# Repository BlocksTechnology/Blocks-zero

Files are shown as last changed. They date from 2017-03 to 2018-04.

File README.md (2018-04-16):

# Blocks zero
In this repository you will find the firmware source code, BOM, STLs of the printed parts and frames for the [Blocks zero 3D printer](http://blockstec.com/zero.html)

# Updating the firmware:
 - Download and install Cura 15.02.1: [Win](http://software.ultimaker.com/old/Cura_15.02.1.exe) / [Mac](http://software.ultimaker.com/old/Cura-15.02.1-MacOS.dmg)
 - Download the [HEX file](http://blockstec.com/downloads/Blocks_zero_1.2.1.hex)
 - Connect your USB printer cable
 - Open Cura and select menu "Machine" -> "Install custom firmware"
 - Select the downloaded HEX file.
 - Wait for the upload to finish and press "OK"

In case the update does not start, please verify the "Serial port" and "Baudrate" (250000) settings in the menu "Machine" -> "Machine settings".

# Changelog:
V1.2.1:
 - Homing after print bug solved

V1.2:
 - USB communication bug solved
 - Baudrate changed to 250000

V1.1:
 - New load/unload filament routine
 - Option to clean the nozzle before bed level
 - Thermal runaway safety feature
 - Filament runout (needs printing new extruder and adding a microswitch to work)
 - Reversed direction of the LCD knob

# License
Blocks one is licensed under a [Creative Commons Attribution-ShareAlike 4.0 International License](http://creativecommons.org/licenses/by-sa/4.0/)

# Firmware
The firmware was based on [Marlin](https://github.com/MarlinFirmware/Marlin) and https://github.com/bq/Marlin

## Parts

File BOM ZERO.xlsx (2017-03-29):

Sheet: BOM zero
 | Bom Blocks Zero
 | ITEM LIST | DESCRIPTION | NOTAS | DATASHEET | LINKS
1 | MEGA 2560 R3 | Arduino
1 | RAMPS 1.4 Board Red For Mega 2560 R3
1 | RepRapDiscount Smart Controller 2004LCD Blue Light
4 | Green A4988 Stepper Motor Driver (+Heatsink,1.5A) | Drivers
3 | NEMA17 Stepper Motor 34mm Long, 1.5A | Motors X,Y,Z
1 | NEMA17 Stepper Motor 40mm Long, 1.2A | Motor Extruder
3 | Bed Spring | Springs for bed
1 | 12V 3010 Cooling Fan | Hotend cooler fan
2 | 12V 5015 Blow Fan | Nozzle/Electronics fan
2 | Bowden Fitting | Fittings PTFE
1 | MK7 Stainless Steel Extrusion Gear | Extruder gear
1 | Closed Loop GT2 Belt - 190 teeth / 380mm | Timming belt for X (hotend)
1 | Closed Loop GT2 Belt - 210 teeth / 420 mm | Timming belt for Y (bed)
2 | 20 teeth GT2 Aluminium Timing Pulley 5mm | pulley X & Y
6 | LM6UU Linear Bearing | X & Y
4 | LM8UU Linear Bearing | Z
12 | Timing Belt Idler Pulley F625Z Flanged Ball Bearing | Idlers
1 | 608ZZ Ball Bearing | Extrusor
2 | High Frequency Chrome Plated Smooth Rod 8mm - 235mm | Z
2 | High Frequency Chrome Plated Smooth Rod 6mm - 200mm | Y
2 | High Frequency Chrome Plated Smooth Rod 6mm - 183mm | X
1 | Acrilic frames | 6 frames
9 | Printed parts
1 | Threaded rod M5 200mm | Z
2 | Black cable guides (50 & 30cm) | Cables |  |  | TME (http://www.tme.eu/en/details/cyg-pet-10-bk_box/polyester-conduits/cyg/cyg-pet10-box/)
3 | 30 mm silicone tube | Z /fan spacer
2 | 10 mm silicone tube | LCD spacer
1 | DC power jack | 5,5x2,1mm 12V/6A |  |  | https://mauser.pt/catalog/product_info.php?cPath=1874_640_387_1155&products_id=56723
1 | Power switch | 20mm white |  |  | https://mauser.pt/catalog/product_info.php?cPath=324_1401_1402&products_id=66105
20 | Zip ties | white - 100mm |  |  | TME (http://www.tme.eu/en/details/bmb1025/cable-ties/bm-group/)
2 | Bulldog clips | bed clamps
2 | Extruder springs | Extruder
1 | Caixa de junção | fans/ Power |  |  | TME (http://www.tme.eu/en/details/dg235-5.0-02p/pcb-terminal-blocks/degson-electronics/dg235-50-02p-11-00ah/)
1 | Hot End
1 | Autocolantes Blocks logo | Stickers
21 | Etiquetas | Cable tags
1 | Allen key 1.5mm | Bossard |  |  | TME (http://www.tme.eu/en/details/b1.5_bn1169/hex-and-torx-keys/bossard/1380605/)
1 | Allen key 2 mm | Bossard |  |  | TME (http://www.tme.eu/en/details/b2_bn1169/hex-and-torx-keys/bossard/1380613/)
1 | Allen key 2.5mm | Bossard |  |  | TME (http://www.tme.eu/en/details/b2.5_bn1169/hex-and-torx-keys/bossard/m25bn1169/)
1 | Allen key 3mm | Carl Kammerling |  |  | TME (http://www.tme.eu/en/details/ck-441103/hex-and-torx-keys/carl-kammerling/t4411-03/)
 | Screws Nuts Washers
35 | M3 16 mm | Bossard | BN17 |  | TME (http://www.tme.eu/pt/details/b3x16_bn17/cavilhas/bossard/3646125/)
23 | M3 8 mm | Bossard | BN17 |  | TME (http://www.tme.eu/pt/details/b3x8_bn17/cavilhas/bossard/3186761/)
1 | M3 30 mm | Bossard | BN17 |  | TME (http://www.tme.eu/pt/details/b3x30_bn17/cavilhas/bossard/3646128/)
9 | M3 10 mm | Bossard | BN17 |  | TME (http://www.tme.eu/pt/details/b3x10_bn17/cavilhas/bossard/5503267/)
4 | M3 20 mm | Bossard | BN17 |  | TME (http://www.tme.eu/pt/details/b3x20_bn17/cavilhas/bossard/3646126/)
1 | M3 40 mm | Fabory / Bossard | BN613 | FABORY (https://www.fabory.com/pt/fixacao/produtos-sextavados-interiores/parafuso-cabeca-cilindrica-sextavado-interior-din-912-aco-inoxidavel-a2-min-50-m3x40/p/510500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) | TME (http://www.tme.eu/pt/details/b3x40_bn613/cavilhas/bossard/1406795/)
5 | M3 50 mm | Fabory / Bossard | BN613 | FABORY (https://www.fabory.com/pt/fixacao/produtos-sextavados-interiores/parafuso-cabeca-cilindrica-sextavado-interior-din-912-aco-inoxidavel-a2-70-m3x50/p/51050030050) | TME (http://www.tme.eu/pt/details/b3x50_bn613/cavilhas/bossard/1746189/)
4 | M2 8 mm | Bossard | BN11 |  | TME (http://www.tme.eu/pt/details/b2x8_bn11/cavilhas/bossard/m2x8bn11/)
2 | M2 12 mm | Bossard | BN612 |  | TME (http://www.tme.eu/pt/details/b2x12_bn612/cavilhas/bossard/1233726/)
6 | M5 25 mm | Bossard | BN17 |  | TME (http://www.tme.eu/pt/details/b5x25_bn17/cavilhas/bossard/1019783/)
2 | M4 20mm | Bossard | BN17 |  | TME (http://www.tme.eu/pt/details/b4x20_bn17/cavilhas/bossard/1019708/)
50 | M3 nut | Bossard | BN117 |  | TME (http://www.tme.eu/pt/details/b3_bn117/porcas/bossard/1874659/)
7 | M5 nut | Bossard | BN124 |  | TME (http://www.tme.eu/pt/details/b5_bn124/porcas/bossard/m5bn124/)
2 | M2 nut | Bossard | BN109 |  | TME (http://www.tme.eu/pt/details/b2_bn109/porcas/bossard/m2bn109/)
5 | M5 washer | Bossard | BN670 |  | TME (http://www.tme.eu/pt/details/b5_bn670/arruelas/bossard/1253212/)
1 | M5 spacer | Dremec | 5.3x8mm |  | TME (http://www.tme.eu/pt/details/dr3110_5.3x8/espacadores-metalicos/dremec/311053x08/)
 | Cables | Comprimento (cm) | Terminação
1 | Endstop X | 95 cm | Jst e Fim de Curso | https://www.omron.com/ecb/products/pdf/en-d2f.pdf | http://www.tme.eu/pt/details/d2f-01fl/microcomutadores-de-conexao/omron/
1 | Endstop Y | 15 cm | Jst e Fim de Curso | https://www.omron.com/ecb/products/pdf/en-d2f.pdf | http://www.tme.eu/pt/details/d2f-01fl/microcomutadores-de-conexao/omron/
1 | Endstop Z | 15 cm | Jst e Fim de Curso | https://www.omron.com/ecb/products/pdf/en-d2f.pdf | http://www.tme.eu/pt/details/d2f-01fl/microcomutadores-de-conexao/omron/
1 | Fan 30x30 | 95 cm | Preto/vermelho
1 | Blower 5010 | 20 cm | Preto/vermelho
1 | Blower 5010 | 95 cm | Preto/Branco
1 | Motor X | 40 a 70 cm | Normal
1 | Motor Y | 15 a 30 cm | Normal
1 | Motor Z | 15 a 30 cm | Normal
1 | Motor Ex | 40 a 70 cm | Normal
1 | Heater Hotend | 90 a 100 cm | Normal
1 | Sensor temp hotend | 90 a 100 cm | Jst
 | Etiquetas | Código
 | Endstop X | H.4-X
 | Endstop Y | B.4-Y
 | Endstop Z | P.1-Z
 | Blower Peça | J.1
 | Fan hotend | J.2
 | Blower Electrónica | P.7
 | Hotend heater
 | Termistor

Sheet: WEAS cablagem
 | Pedido de Orçamento para Cablagem da BLOCKS zero
 |  | Comprimento (cm) | Terminações | Datasheet
 | Cables
1 | Endstop X | 95 | Jst e Fim de Curso (Com/NC) | https://www.omron.com/ecb/products/pdf/en-d2f.pdf
1 | Endstop Y | 15 | Jst e Fim de Curso (Com/NC) | https://www.omron.com/ecb/products/pdf/en-d2f.pdf
1 | Endstop Z | 15 | Jst e Fim de Curso (Com/NC) | https://www.omron.com/ecb/products/pdf/en-d2f.pdf
 | Conjunto Power | 2x20 cm + 7 cm | 12V/6A requisitos mínimos
1 | DC power plug | ver fotos abaixo | 2 x Soldar e Manga termoretráctil | http://www.cliffuk.co.uk/products/dcconnectors/FC681492.pdf
1 | Power switch white | ver fotos abaixo | 2 x Soldar e Manga termoretráctil | http://www.bulgin.com/media/bulgin/data/A_Rocker%20Switch.pdf
1 | Caixa de junção | ver fotos abaixo | 4 x Soldar e Manga termoretráctil | http://www.degson.com/20081120/epdf/1175.pdf
1 | Ficha verde Ramps | ver fotos abaixo | 2 x Esmagar com parafuso | fornecida com o Ramps

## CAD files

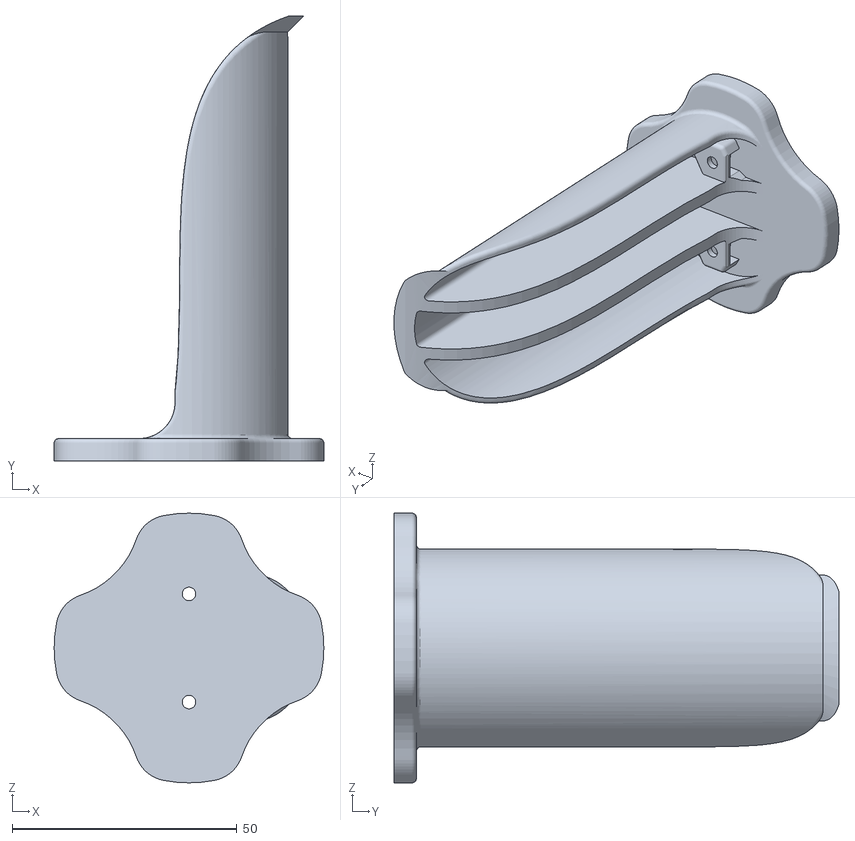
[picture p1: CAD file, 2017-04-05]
STL_Files/Spool V2.stl
60.0 x 99.0 x 60.0

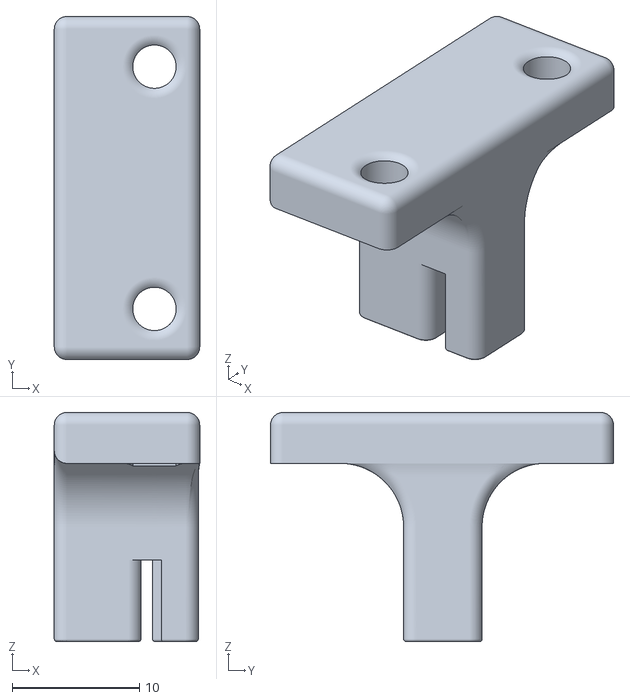
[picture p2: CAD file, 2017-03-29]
STL_Files/belgt fixer Y.stl
11.4 x 26.9 x 18.0

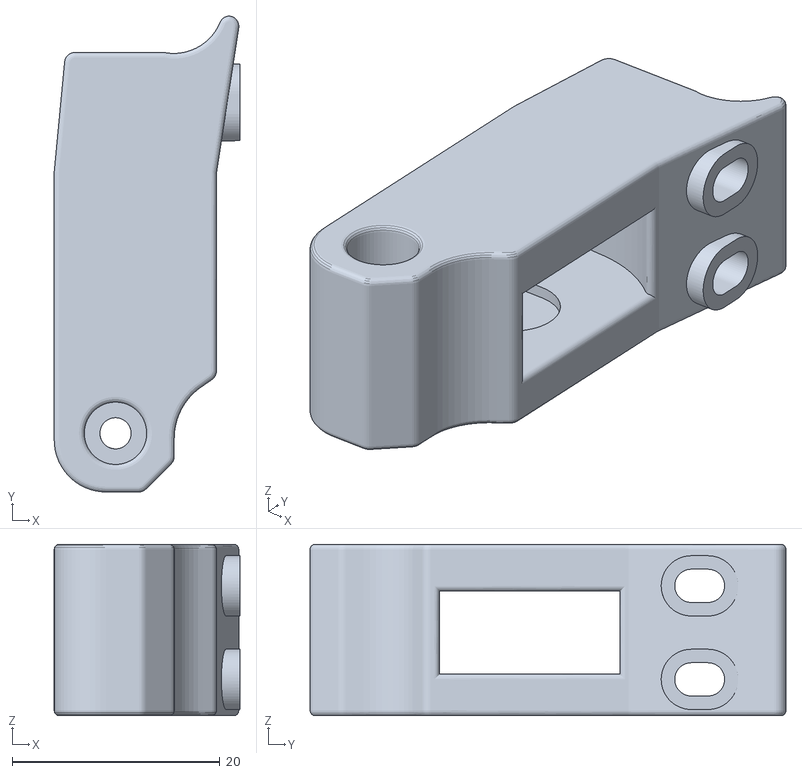
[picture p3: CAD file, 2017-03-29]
STL_Files/Extrusor Idler.stl
17.9 x 45.8 x 16.5

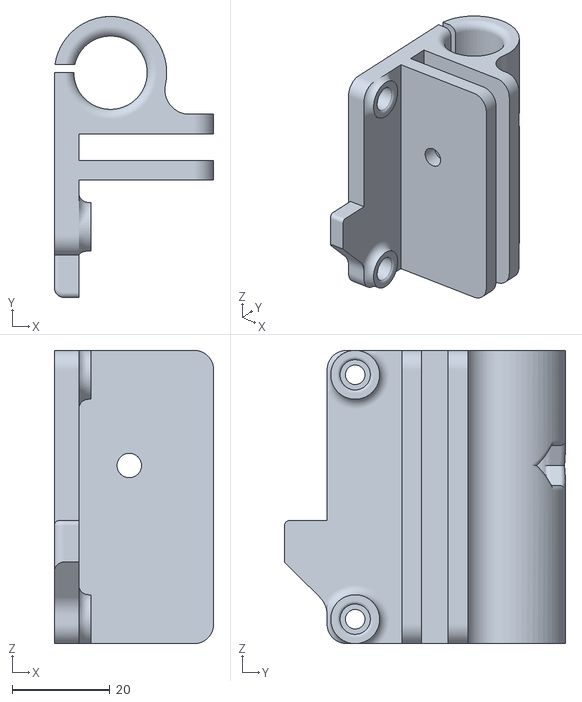
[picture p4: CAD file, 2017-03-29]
STL_Files/XZ left.stl
32.6 x 57.5 x 60.0

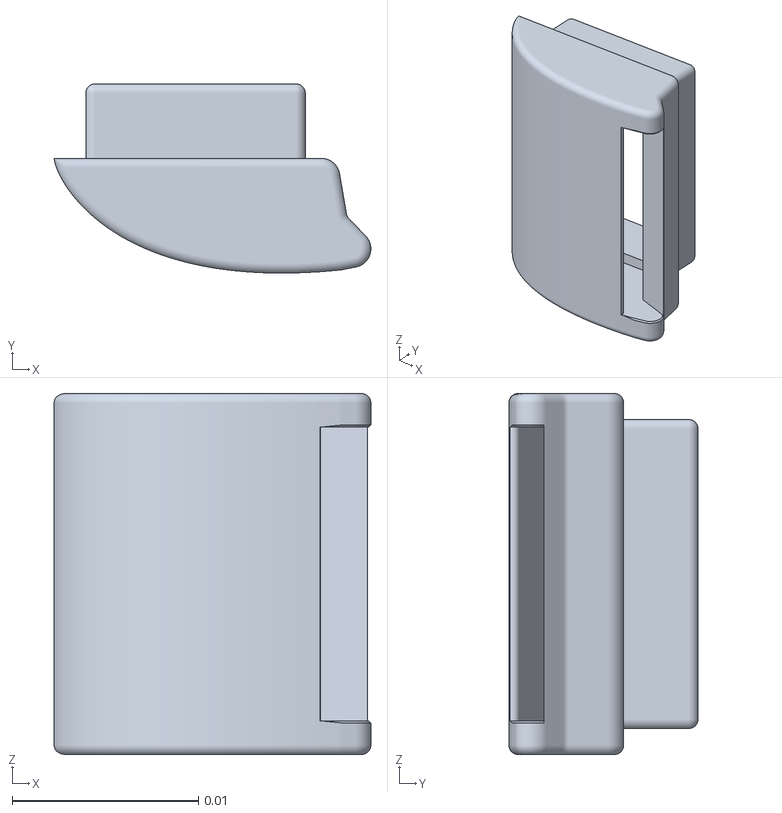
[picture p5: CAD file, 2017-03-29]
STL_Files/Fan Duct.stl
0.017 x 0.0102 x 0.0194

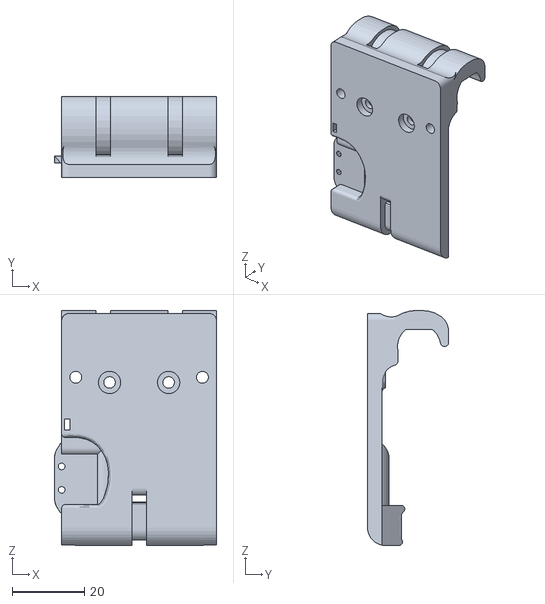
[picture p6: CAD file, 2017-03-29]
STL_Files/X carriage.stl
45.0 x 22.5 x 65.2

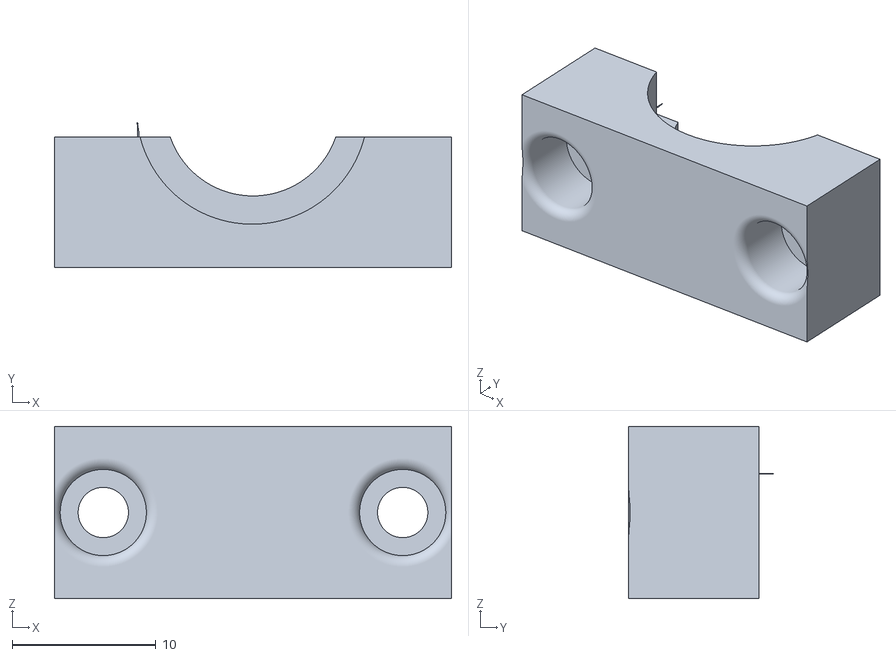
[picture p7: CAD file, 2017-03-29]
STL_Files/Hot end fixer I3.stl
27.6 x 10.1 x 12.0

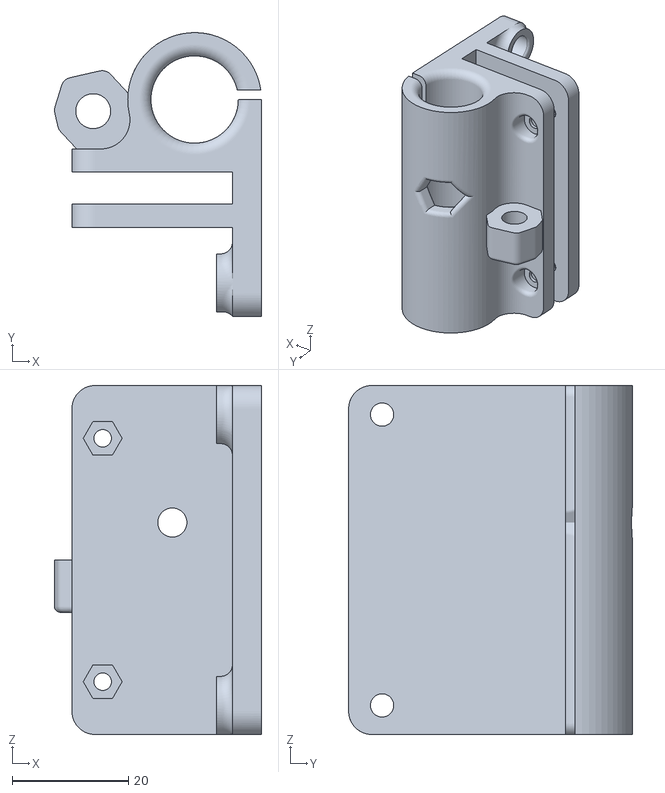
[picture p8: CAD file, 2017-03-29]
STL_Files/XZ right.stl
35.6 x 48.8 x 60.0

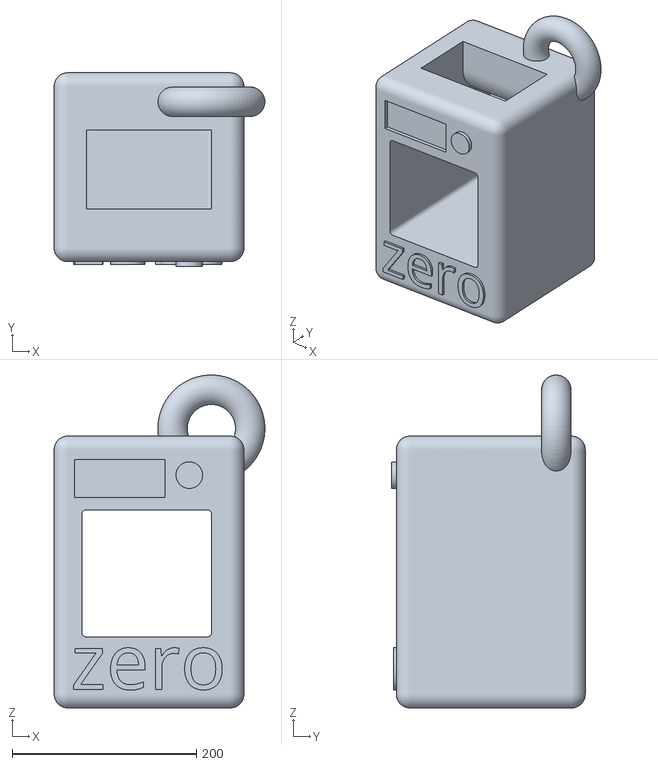
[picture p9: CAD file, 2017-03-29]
STL_Files/porta chaves zero.stl
228.7 x 210.0 x 361.2

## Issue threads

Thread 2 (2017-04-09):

Fan is always on

mamoit, 2017-04-09:
It does not turn off, even if the extruder is cool.
It seems to be always running full steam ahead.

pdluke, 2017-04-13:
I think it is by design. There are many kits that have the extruder fan running on full speed.
Also there is no possibility to control this fan as it is connected directly to the power supply and not to the control board.

Closed 2019-06-08.

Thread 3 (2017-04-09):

Marlin's GPL3 not honored

mamoit, 2017-04-09:
No license provided.

mamoit, 2018-04-16:
This is solved in [the new repository](https://github.com/BlocksTechnology/Blocks-Firmware/tree/zero)

Closed 2018-04-16.

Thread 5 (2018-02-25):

Y axis is actually around 133 long, not 140

mamoit, 2018-02-25:
It says everywhere that the axis is 140mm long, and all the configuration is set accordingly, but the axis is actually not that long, it is 133mm long (at least on the indiegogo version).
This causes the bed to ram into the acrylic case every time it tries to go to it's limits.
A safer option is to set the limits to 13cm, losing 1cm but ensuring that the virtual endstop of Y+ is not rammed into.

choschiba, 2018-04-16:
I‘ve discovered the same thing actually too. And on the z axis I cannot go higher than about 110mm!
I have that Indigogo version.
Is it possible to update the firmware to the newest version? Have you tried?

mamoit, 2018-04-16:
Since posting this issue I actually got hired by Blocks, so now I have a better insight on this.
The problem is that the production version and the indiegogo version are physically different since the axis got a little bit longer in the latter.
This repository holds the code for the Production version of the Blocks Zero.

I have fixed this issue in [my version of Marlin](https://github.com/mamoit/Marlin/tree/bz-1.1.8) (which is just the up to date vanilla version tuned for the indiegogo version of the Blocks Zero), but it lacks some of the tweaks implemented in the Blocks code, such as the filament change routines.

Another option is to change the values for `Y_MAX_POS` and `Z_MAX_POS` in the [`Configuration.h`](https://github.com/BlocksTechnology/Blocks-zero/blob/master/Firmware_1.2/Marlin/Configuration.h#L345) and flash your printer with it, this way you can preserve the Blocks firmware features, and not have the printer hit the bed the limits.

Let me know if you need some help.

Closed 2019-07-09.

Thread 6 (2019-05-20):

I don't know why I can't print.

3dle, 2019-05-20:
The printer can return to the origin, the slice of the model is normal, that is, when printing, the motor does not move, the progress bar does not move, the expansion board has a light flashing, do not know what can not print.

mamoit, 2019-05-20:
Hello, it seems like you may have a hardware issue or some sort of miswiring.
Has the printer worked before or did you just assemble it?
Please contact us through http://blockstec.com/support.html so that we can provide you with troubleshooting support, you can contact us in either English or Portuguese.

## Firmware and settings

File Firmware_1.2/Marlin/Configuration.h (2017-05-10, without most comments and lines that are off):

#define CONFIGURATION_H
#include "boards.h"
#ifdef USE_AUTOMATIC_VERSIONING
  #include "_Version.h"
#else
  #include "Default_Version.h"
#endif
#define STRING_SPLASH_LINE1 SHORT_BUILD_VERSION // will be shown during bootup in line 1
#define STRING_VERSION_CONFIG_H __DATE__ " " __TIME__ // build date and time
#define STRING_CONFIG_H_AUTHOR "(Blocks, zero 1.2.1)" // Who made the changes.
#define SERIAL_PORT 0
#define BAUDRATE 250000
  #define MOTHERBOARD 33
#define EXTRUDERS 1
#define POWER_SUPPLY 1
#define TEMP_SENSOR_0 10
#define TEMP_SENSOR_1 0
#define TEMP_SENSOR_2 0
#define TEMP_SENSOR_BED 0
#define MAX_REDUNDANT_TEMP_SENSOR_DIFF 10
#define TEMP_RESIDENCY_TIME 10  // (seconds)
#define TEMP_HYSTERESIS 3       // (degC) range of +/- temperatures considered "close" to the target one
#define TEMP_WINDOW     1       // (degC) Window around target to start the residency timer x degC early.
#define HEATER_0_MINTEMP 5
#define HEATER_1_MINTEMP 5
#define HEATER_2_MINTEMP 5
#define BED_MINTEMP 5
#define HEATER_0_MAXTEMP 270
#define HEATER_1_MAXTEMP 270
#define HEATER_2_MAXTEMP 270
#define BED_MAXTEMP 110
#define PIDTEMP
#define BANG_MAX 255 // limits current to nozzle while in bang-bang mode; 255=full current
#define PID_MAX BANG_MAX // limits current to nozzle while PID is active (see PID_FUNCTIONAL_RANGE below); 255=full current
  #define PID_FUNCTIONAL_RANGE 10 // If the temperature difference between the target temperature and the actual temperature
  #define PID_INTEGRAL_DRIVE_MAX PID_MAX  //limit for the integral term
  #define K1 0.95 //smoothing factor within the PID
  #define PID_dT ((OVERSAMPLENR * 10.0)/(F_CPU / 64.0 / 256.0)) //sampling period of the temperature routine
    #define  DEFAULT_Kp 22.2
    #define  DEFAULT_Ki 1.08
    #define  DEFAULT_Kd 114
#define MAX_BED_POWER 255 // limits duty cycle to bed; 255=full current
#define PREVENT_DANGEROUS_EXTRUDE
#define EXTRUDE_MINTEMP 170
#define EXTRUDE_MAXLENGTH (X_MAX_LENGTH+Y_MAX_LENGTH) //prevent extrusion of very large distances.
#define THERMAL_RUNAWAY_PROTECTION_PERIOD 40 //in seconds
#define THERMAL_RUNAWAY_PROTECTION_HYSTERESIS 4 // in degree Celsius
#define THERMAL_RUNAWAY_PROTECTION_BED_PERIOD 20 //in seconds
#define THERMAL_RUNAWAY_PROTECTION_BED_HYSTERESIS 2 // in degree Celsius
#define ENDSTOPPULLUPS // Comment this out (using // at the start of the line) to disable the endstop pullup resistors
  #define ENDSTOPPULLUP_XMAX
  #define ENDSTOPPULLUP_YMAX
  #define ENDSTOPPULLUP_ZMAX
  #define ENDSTOPPULLUP_XMIN
  #define ENDSTOPPULLUP_YMIN
  #define ENDSTOPPULLUP_ZMIN
const bool X_MIN_ENDSTOP_INVERTING = true; // set to true to invert the logic of the endstop.
const bool Y_MIN_ENDSTOP_INVERTING = true; // set to true to invert the logic of the endstop.
const bool Z_MIN_ENDSTOP_INVERTING = true; // set to true to invert the logic of the endstop.
const bool X_MAX_ENDSTOP_INVERTING = true; // set to true to invert the logic of the endstop.
const bool Y_MAX_ENDSTOP_INVERTING = true; // set to true to invert the logic of the endstop.
const bool Z_MAX_ENDSTOP_INVERTING = true; // set to true to invert the logic of the endstop.
#if defined(COREXY) && !defined(DISABLE_MAX_ENDSTOPS)
  #define DISABLE_MAX_ENDSTOPS
#endif
#define X_ENABLE_ON 0
#define Y_ENABLE_ON 0
#define Z_ENABLE_ON 0
#define E_ENABLE_ON 0 // For all extruders
#define DISABLE_X false
#define DISABLE_Y false
#define DISABLE_Z false
#define DISABLE_E false // For all extruders
#define DISABLE_INACTIVE_EXTRUDER true //disable only inactive extruders and keep active extruder enabled
#define INVERT_X_DIR true    // for Mendel set to false, for Orca set to true
#define INVERT_Y_DIR false    // for Mendel set to true, for Orca set to false
#define INVERT_Z_DIR true     // for Mendel set to false, for Orca set to true
#define INVERT_E0_DIR false   // for direct drive extruder v9 set to true, for geared extruder set to false
#define INVERT_E1_DIR false    // for direct drive extruder v9 set to true, for geared extruder set to false
#define INVERT_E2_DIR false   // for direct drive extruder v9 set to true, for geared extruder set to false
#define X_HOME_DIR -1
#define Y_HOME_DIR -1
#define Z_HOME_DIR -1
#define min_software_endstops true // If true, axis won't move to coordinates less than HOME_POS.
#define max_software_endstops true  // If true, axis won't move to coordinates greater than the defined lengths below.
#define X_MAX_POS 120
#define X_MIN_POS 0
#define Y_MAX_POS 140
#define Y_MIN_POS 0
#define Z_MAX_POS 120
#define Z_MIN_POS 0
#define X_MAX_LENGTH (X_MAX_POS - X_MIN_POS)
#define Y_MAX_LENGTH (Y_MAX_POS - Y_MIN_POS)
#define Z_MAX_LENGTH (Z_MAX_POS - Z_MIN_POS)
#define Z_PROBE_REPEATABILITY_TEST  // If not commented out, Z-Probe Repeatability test will be included if Auto Bed Leveling is Enabled.
#define MANUAL_X_HOME_POS 0
#define MANUAL_Y_HOME_POS 0
#define MANUAL_Z_HOME_POS 0
#define NUM_AXIS 4 // The axis order in all axis related arrays is X, Y, Z, E
#define HOMING_FEEDRATE {2000, 2000, 180, 0}  //{50*60, 50*60, 4*60, 0} set the homing speeds (mm/min)
#define DEFAULT_AXIS_STEPS_PER_UNIT   {80, 80, 4000,97}  // default steps per unit for Ultimaker
#define DEFAULT_MAX_FEEDRATE          {250, 250, 3, 50}    // (mm/sec)
#define DEFAULT_MAX_ACCELERATION      {3000,3000,100,10000}    // X, Y, Z, E maximum start speed for accelerated moves. E default values are good for Skeinforge 40+, for older versions raise them a lot.
#define DEFAULT_ACCELERATION          2000    // X, Y, Z and E max acceleration in mm/s^2 for printing moves
#define DEFAULT_RETRACT_ACCELERATION  1000   // X, Y, Z and E max acceleration in mm/s^2 for retracts
#define DEFAULT_XYJERK                20.0    // (mm/sec)
#define DEFAULT_ZJERK                 0.4     // (mm/sec)
#define DEFAULT_EJERK                 5.0    // (mm/sec)
#define CUSTOM_M_CODES
  #define CUSTOM_M_CODE_SET_Z_PROBE_OFFSET 851
  #define Z_PROBE_OFFSET_RANGE_MIN -15
  #define Z_PROBE_OFFSET_RANGE_MAX -5
#define FILAMENT_RUNOUT_SENSOR
#define FIL_RUNOUT_PIN 4
#define FIL_RUNOUT_INVERTING false
#define EXTRUSION_SPEED 200
#define LEVEL_PLATE_TEMP_PROTECTION 60
#define Change_Filament_Target_Temp 220
#define FILAMENT_EXTRUSION_LENGTH 30
#define FILAMENT_UNLOAD_EXTRUSION_LENGTH 5
#define FILAMENT_UNLOAD_RETRACTION_LENGTH 600
#define PREHEAT_HOTEND_TEMP 180
#define PREHEAT_FAN_SPEED 0
#define COOLDOWN_FAN_SPEED 255
#define XY_TRAVEL_SPEED 8000    // X and Y axis travel speed between probes and Witbox movements, in mm/min
#define PLA_PREHEAT_HOTEND_TEMP 180
#define PLA_PREHEAT_HPB_TEMP 70
#define PLA_PREHEAT_FAN_SPEED 255   // Insert Value between 0 and 255
#define ABS_PREHEAT_HOTEND_TEMP 240
#define ABS_PREHEAT_HPB_TEMP 100
#define ABS_PREHEAT_FAN_SPEED 255   // Insert Value between 0 and 255
#define SDSUPPORT // Enable SD Card Support in Hardware Console
#define REPRAP_DISCOUNT_SMART_CONTROLLER
 #define ULTIPANEL
 #define NEWPANEL
  #define SDSUPPORT
  #define ULTRA_LCD
    #define LCD_WIDTH 20
    #define LCD_HEIGHT 4
#define SOFT_PWM_SCALE 0
#define FILAMENT_SENSOR_EXTRUDER_NUM	0  //The number of the extruder that has the filament sensor (0,1,2)
#define MEASUREMENT_DELAY_CM			14  //measurement delay in cm.  This is the distance from filament sensor to middle of barrel
#define DEFAULT_NOMINAL_FILAMENT_DIA  3.0  //Enter the diameter (in mm) of the filament generally used (3.0 mm or 1.75 mm) - this is then used in the slicer software.  Used for sensor reading validation
#define MEASURED_UPPER_LIMIT          3.30  //upper limit factor used for sensor reading validation in mm
#define MEASURED_LOWER_LIMIT          1.90  //lower limit factor for sensor reading validation in mm
#define MAX_MEASUREMENT_DELAY			20  //delay buffer size in bytes (1 byte = 1cm)- limits maximum measurement delay allowable (must be larger than MEASUREMENT_DELAY_CM  and lower number saves RAM)
#define DEFAULT_MEASURED_FILAMENT_DIA  DEFAULT_NOMINAL_FILAMENT_DIA  //set measured to nominal initially
#include "Configuration_adv.h"
#include "thermistortables.h"

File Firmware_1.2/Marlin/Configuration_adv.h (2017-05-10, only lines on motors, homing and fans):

#define CONTROLLERFAN_PIN -1 //Pin used for the fan to cool controller (-1 to disable)
#define EXTRUDER_0_AUTO_FAN_PIN   -1
#define EXTRUDER_1_AUTO_FAN_PIN   -1
#define EXTRUDER_2_AUTO_FAN_PIN   -1
#define X_HOME_RETRACT_MM 5
#define Y_HOME_RETRACT_MM 5
#define Z_HOME_RETRACT_MM 2
#define MICROSTEP1 LOW,LOW
#define MICROSTEP2 HIGH,LOW
#define MICROSTEP4 LOW,HIGH
#define MICROSTEP8 HIGH,HIGH
#define MICROSTEP16 HIGH,HIGH
#define MICROSTEP_MODES {16,16,16,16,16} // [1,2,4,8,16]
#define DIGIPOT_MOTOR_CURRENT {135,135,135,135,135} // Values 0-255 (RAMBO 135 = ~0.75A, 185 = ~1A)
#define DIGIPOT_I2C_MOTOR_CURRENTS {1.0, 1.0, 1.0, 1.0, 1.0, 1.0, 1.0, 1.0}

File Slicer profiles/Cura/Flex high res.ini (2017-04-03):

[profile]
layer_height = 0.1
wall_thickness = 1.2
retraction_enable = True
solid_layer_thickness = 1
fill_density = 20
nozzle_size = 0.4
print_speed = 40
print_temperature = 225
print_temperature2 = 0
print_temperature3 = 0
print_temperature4 = 0
print_temperature5 = 0
print_bed_temperature = 70
support = None
platform_adhesion = Brim
support_dual_extrusion = Both
wipe_tower = False
wipe_tower_volume = 15
ooze_shield = False
filament_diameter = 1.75
filament_diameter2 = 0
filament_diameter3 = 0
filament_diameter4 = 0
filament_diameter5 = 0
filament_flow = 100.0
retraction_speed = 45
retraction_amount = 5.5
retraction_dual_amount = 16.5
retraction_min_travel = 1.5
retraction_combing = All
retraction_minimal_extrusion = 0.02
retraction_hop = 0.0
bottom_thickness = 0.24
layer0_width_factor = 100
object_sink = 0.0
overlap_dual = 0.15
travel_speed = 150.0
bottom_layer_speed = 20
infill_speed = 0
solidarea_speed = 0
inset0_speed = 0
insetx_speed = 0
cool_min_layer_time = 5
fan_enabled = True
skirt_line_count = 1
skirt_gap = 3.0
skirt_minimal_length = 150.0
fan_full_height = 0.5
fan_speed = 90
fan_speed_max = 100
cool_min_feedrate = 10
cool_head_lift = False
solid_top = True
solid_bottom = True
fill_overlap = 15
support_type = Lines
support_angle = 60
support_fill_rate = 10
support_xy_distance = 0.7
support_z_distance = 0.2
spiralize = False
simple_mode = False
brim_line_count = 10
raft_margin = 5.0
raft_line_spacing = 3.0
raft_base_thickness = 0.3
raft_base_linewidth = 1.0
raft_interface_thickness = 0.27
raft_interface_linewidth = 0.4
raft_airgap_all = 0.0
raft_airgap = 0.22
raft_surface_layers = 2
raft_surface_thickness = 0.27
raft_surface_linewidth = 0.4
fix_horrible_union_all_type_a = True
fix_horrible_union_all_type_b = False
fix_horrible_use_open_bits = False
fix_horrible_extensive_stitching = False
plugin_config = 
object_center_x = -1
object_center_y = -1

[alterations]
start.gcode = ;Sliced at: {day} {date} {time}
	;Basic settings: Layer height: {layer_height} Walls: {wall_thickness} Fill: {fill_density}
	;Print time: {print_time}
	;Filament used: {filament_amount}m {filament_weight}g
	;Filament cost: {filament_cost}
	;M190 S{print_bed_temperature} ;Uncomment to add your own bed temperature line
	;M109 S{print_temperature} ;Uncomment to add your own temperature line
	G21        ;metric values
	G90        ;absolute positioning
	M82        ;set extruder to absolute mode
	M107       ;start with the fan off
	G28 X0 Y0  ;move X/Y to min endstops
	G28 Z0     ;move Z to min endstops
	G1 Z15.0 F{travel_speed} ;move the platform down 15mm
	G92 E0                  ;zero the extruded length
	G1 F200 E3              ;extrude 3mm of feed stock
	G92 E0                  ;zero the extruded length again
	G1 F{travel_speed}
	;Put printing message on LCD screen
	M117 Printing...
end.gcode = ;End GCode
	M104 S0                     ;extruder heater off
	M140 S0                     ;heated bed heater off (if you have it)
	G91                                    ;relative positioning
	G1 E-1 F300                            ;retract the filament a bit before lifting the nozzle, to release some of the pressure
	G1 Z+0.5 E-5 X-20 Y-20 F{travel_speed} ;move Z up a bit and retract filament even more
	G28 X0 Y0                              ;move X/Y to min endstops, so the head is out of the way
	M84                         ;steppers off
	G90                         ;absolute positioning
	;{profile_string}
start2.gcode = ;Sliced at: {day} {date} {time}
	;Basic settings: Layer height: {layer_height} Walls: {wall_thickness} Fill: {fill_density}
	;Print time: {print_time}
	;Filament used: {filament_amount}m {filament_weight}g
	;Filament cost: {filament_cost}
	;M190 S{print_bed_temperature} ;Uncomment to add your own bed temperature line
	;M104 S{print_temperature} ;Uncomment to add your own temperature line
	;M109 T1 S{print_temperature2} ;Uncomment to add your own temperature line
	;M109 T0 S{print_temperature} ;Uncomment to add your own temperature line
	G21        ;metric values
	G90        ;absolute positioning
	M107       ;start with the fan off
	G28 X0 Y0  ;move X/Y to min endstops
	G28 Z0     ;move Z to min endstops
	G1 Z15.0 F{travel_speed} ;move the platform down 15mm
	T1                      ;Switch to the 2nd extruder
	G92 E0                  ;zero the extruded length
	G1 F200 E10             ;extrude 10mm of feed stock
	G92 E0                  ;zero the extruded length again
	;G1 F200 E-{retraction_dual_amount}
	T0                      ;Switch to the first extruder
	G92 E0                  ;zero the extruded length
	G1 F200 E10             ;extrude 10mm of feed stock
	G92 E0                  ;zero the extruded length again
	G1 F{travel_speed}
	;Put printing message on LCD screen
	M117 Printing...
end2.gcode = ;End GCode
	M104 T0 S0                     ;extruder heater off
	M104 T1 S0                     ;extruder heater off
	M140 S0                     ;heated bed heater off (if you have it)
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

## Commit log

2017-03-29 Blocks zero
    assembly, frames, firmware 1.0, STL
    [BOM ZERO.xlsx, Configuration.h, Configuration_adv.h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]
2017-04-03 Cura profiles
    Addition of the cura print profiles
2017-04-05 Frames corrected
    Updated frames and STLs
    [Frame back Drawing 1.dxf, Frame left Drawing 1.dxf, Frame right Drawing 1.dxf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]
2017-04-07 Pause LCD function correction
    Pause position changed to 5mm,5mm
    First retraction for filament change, changed to 5.5mm
    [Configuration_adv.h]
2017-05-03 Firmware 1.2
    [Configuration.h, Configuration_adv.h, Menu Plans.xlsx]
2017-05-10 Firmnware 1.2.1
    Homing after print bug solved
    [Configuration_adv.h]
2017-05-10 Fimrware 1.2.1
    Correct version display boot screen
    [Configuration.h]
2017-07-13 Update link to firmware
    So people don't download the wrong one and end up with the extruder ramming into the print :smile:
